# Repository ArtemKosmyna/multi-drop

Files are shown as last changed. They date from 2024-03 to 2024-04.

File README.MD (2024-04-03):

# Барабанний Скид для FPV

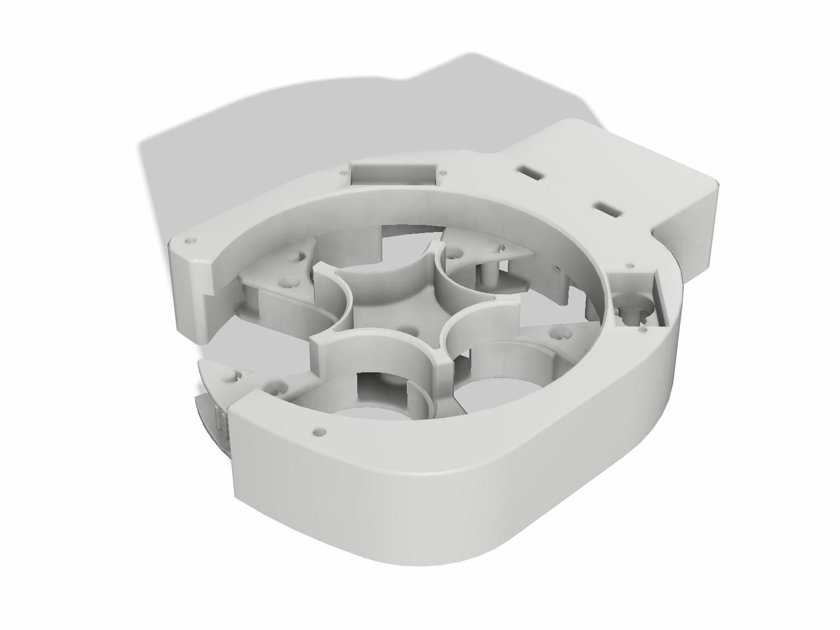
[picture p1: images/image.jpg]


## Огляд

Цей проект є барабанним скидом для FPV, розробленим для скидання 5 предметів. Він може бути монтований на дрон і управляється за допомогою сервопривода. Сам скид складається з двох основних частин: корпусу та барабану. Корпус закріплюється на дроні, тоді як барабан обертається всередині корпусу. В барабані є отвори, через які можуть випадати предмети. Сервопривід забезпечує обертання барабана та відкривання/закривання отворів.

## Інструкції зі збірки

### Налаштування друку

- Підтримка: Відсутня
- Стінки: 4 шари
- Заповнення: 20%
- Верхні/нижні стінки: 4 шари
- Матеріал: PETG

### Матеріали для VOG

- (1) БРФ_1.01.005.010_Корпус с Ардуино на 2 Холла
- (1) БРФ_1,01,005,016_Ревизия плоская
- (1) БРФ_1,01,005,013_Корпус барабана_магнит 5х2
- (2) БРФ_1,01,005,006_Шестерня привода (x,x)
- (5) БРФ_1.01.005.003_Заслонка_5stk
- (1) БРФ_1.01.005.002_Централь
- (1) БРФ_1.01.005.004_Крышка барабана
- (5) БРФ_1.01.005.005_Толкатель_5stk
- (5) БРФ_1.01.005.007_Шестерня ведомая_5stk
- (1) БРФ_1.01.005.012_Крышка под ардуино
- (4) Винти М1.4×4 для Arduino
- (15) Винти M3x8 (DIN 965 (хрест) або DIN 7991 (шестиграник)) - 15 штук

### Матеріали для 40mm

- 

### Електроніка

- (2) Сервоприводи MG-90 360 (без стопера)
- (5) Пружини d=5mm
- (2) Датчик Холла SS49E
- (1) Arduino Nano
- (2) Шлейф 3-жильний 26AWG 1м (Чорний, Червоний, Жовтий)
- (5) Магнит d=5mm, h=2mm
- (2) Термоусадкі 3=mm

### Необхідні інструменти та матеріали

- Викрутка (хрестова або плоска, залежно від кріплення корпусу серво)
- Паяльник і припій
- Електроізоляційна стрічка або термоусаджувальна трубка
- Сервотестер
- Блок живлення на 5 вольт

## Інструкції з прошивки

Цей документ містить інструкції з прошивки для Arduino Nano. Перед початком переконайтесь, що у вас встановлене середовище розробки, яке підтримує вашу Arduino Nano.

### Загальні вимоги

- Встановлене середовище [Arduino IDE](https://www.arduino.cc/en/software) або [PlatformIO](https://platformio.org/platformio-ide) для Arduino.
- USB-кабель для підключення плати до комп'ютера.
- Драйвери для вашої плати, якщо вони потрібні.

### Прошивка для Arduino

1. Відкрийте Arduino IDE.
2. Виберіть `Файл` > `Відкрити...` та знайдіть файл `firmware_(розмір_магніту).ino` у папці `arduino`.
3. Підключіть вашу п

лату Arduino до комп'ютера через USB.
4. Виберіть тип плати та порт у `Інструменти`.
5. Натисніть `Завантажити` для прошивки плати.

## Схема підключення до Arduino

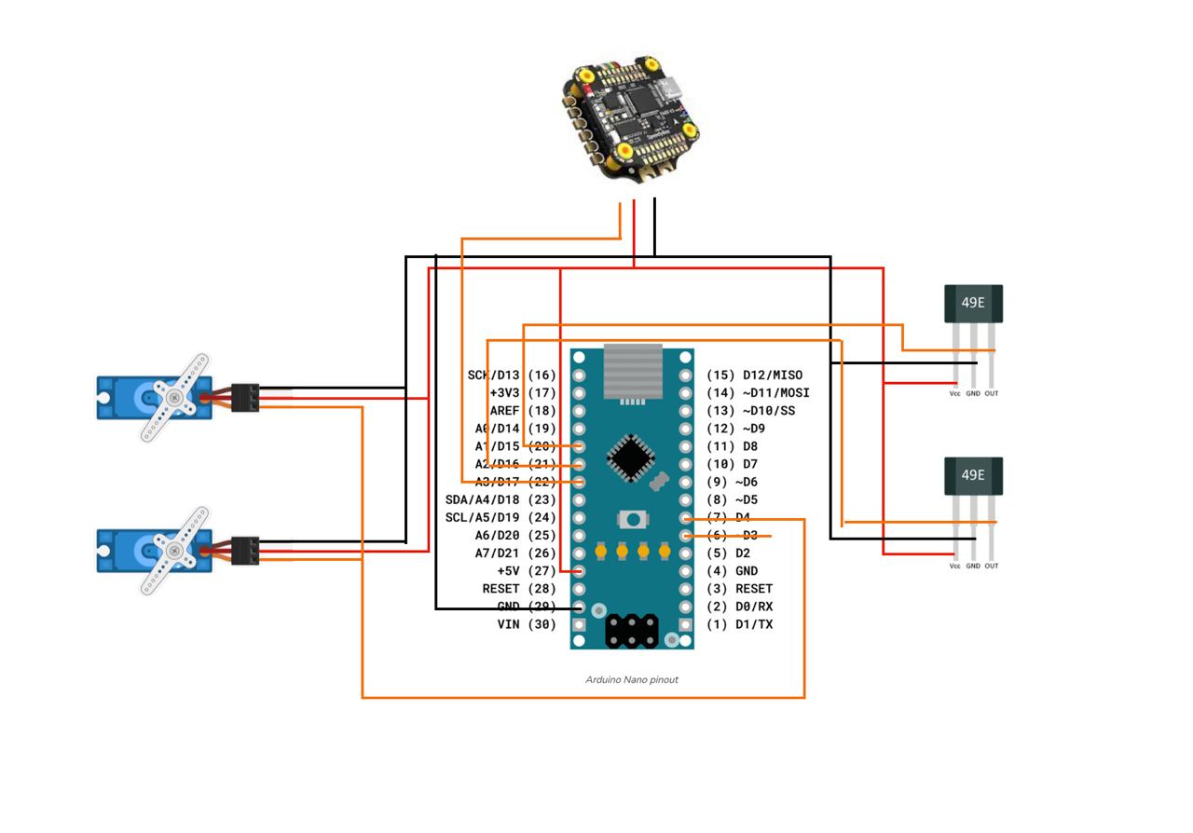
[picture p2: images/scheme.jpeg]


## Схема підключення датчиків положення

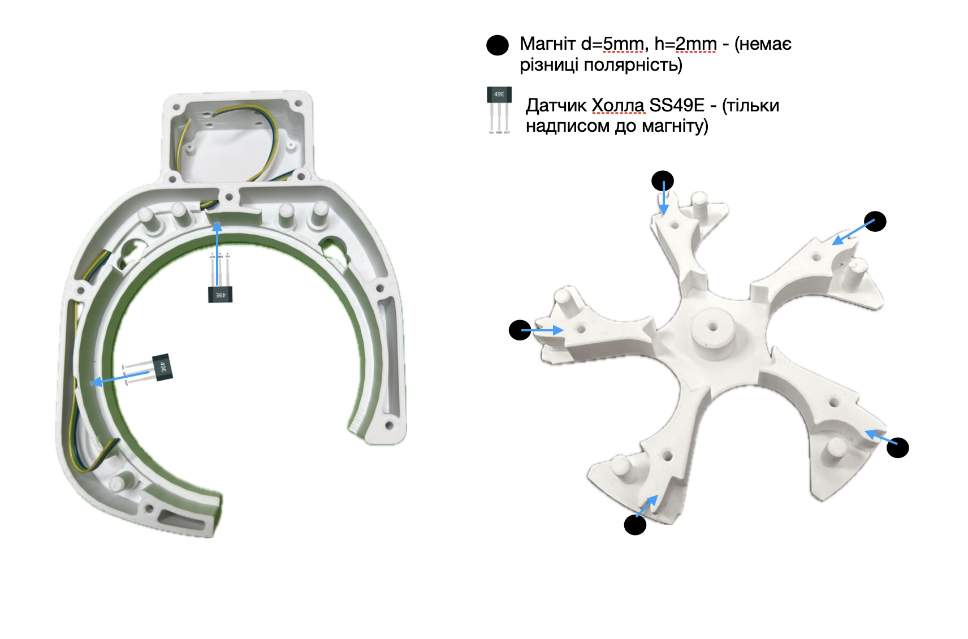
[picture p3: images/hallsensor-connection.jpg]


## Примітки

- Переконайтесь, що вибраний правильний COM-порт для вашої плати перед завантаженням.
- У деяких випадках може бути потрібно натиснути та утримувати кнопку BOOT на платі перед завантаженням або скинути плату безпосередньо після початку завантаження.

Якщо у вас виникають проблеми з підключенням або прошивкою, зверніться до офіційної документації вашої платформи.

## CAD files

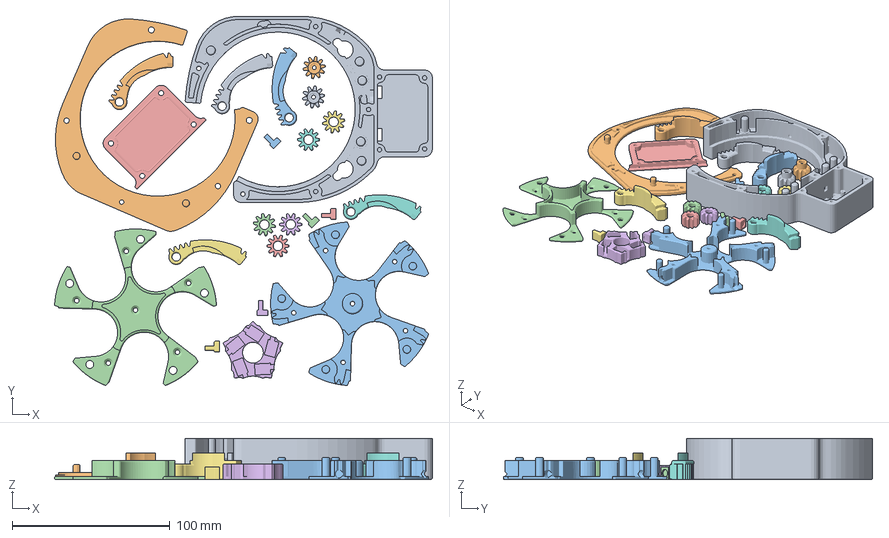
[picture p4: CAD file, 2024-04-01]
3MF/multi-drop-vog-v1.0.0.3mf
239.5 x 234.0 x 26.1 mm
БРФ_1.01.005.010_Корпус с Ардуино на 2 Холла.stl
БРФ_1.01.005.012_Крышка под ардуино.stl
БРФ_1,01,005,013_Корпус барабана_магнит 5х2.stl
БРФ_1.01.005.004_Крышка барабана.stl
БРФ_1,01,005,016_Ревизия плоская.stl
БРФ_1.01.005.002_Централь.stl
БРФ_1.01.005.003_Заслонка_5stk.stl x 5
БРФ_1.01.005.007_Шестерня ведомая_5stk.stl x 5
БРФ_1,01,005,006_Шестерня привода 4,85.stl x 2
БРФ_1.01.005.005_Толкатель_5stk.stl x 5

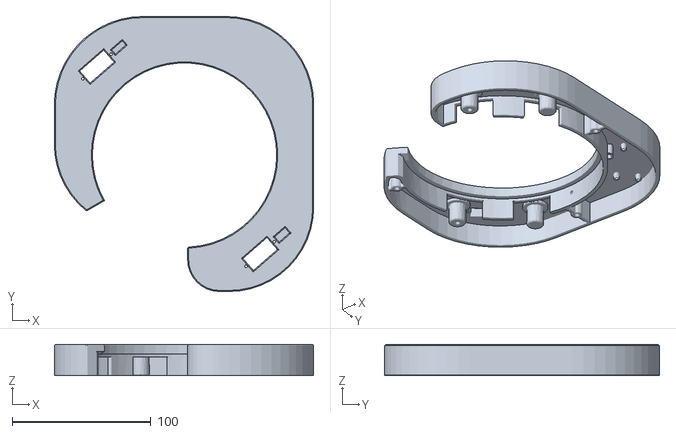
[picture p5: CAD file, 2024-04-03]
STL/40mm/БР_1,02,001,008_ Корпус_Серва.stl
187.2 x 198.5 x 22.4

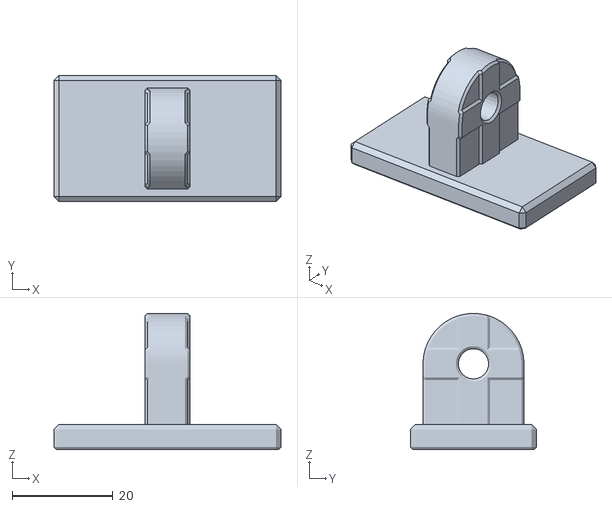
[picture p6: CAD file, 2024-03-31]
STL/VOG/БРФ_1.01.005.014_Кронштейн.stl
45.0 x 25.0 x 27.0

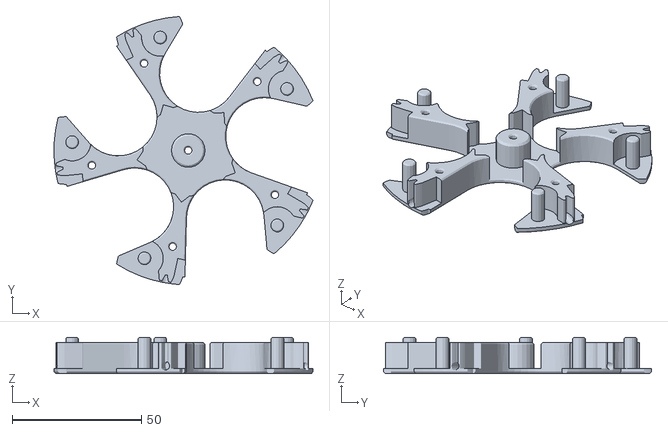
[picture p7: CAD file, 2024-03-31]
STL/VOG/Корпус барабана/БРФ_1,01,005,013_Корпус барабана_магнит 3х6.stl
100.1 x 103.6 x 14.0

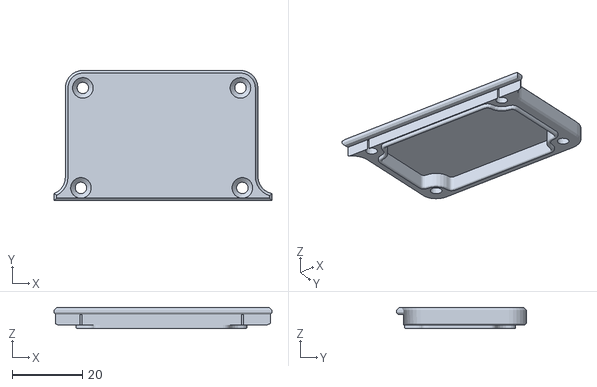
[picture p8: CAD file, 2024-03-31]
STL/VOG/Ревизия/БРФ_1,01,005,016_Ревизия плоская.stl
62.2 x 37.2 x 6.00

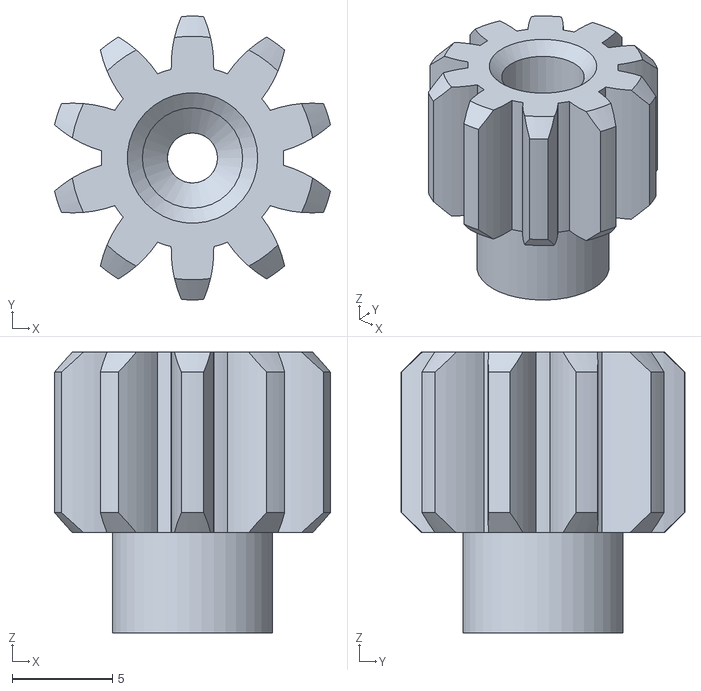
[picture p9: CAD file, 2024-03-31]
STL/VOG/Шестерня/БРФ_1,01,005,006_Шестерня привода 4,9.stl
13.8 x 14.1 x 14.0

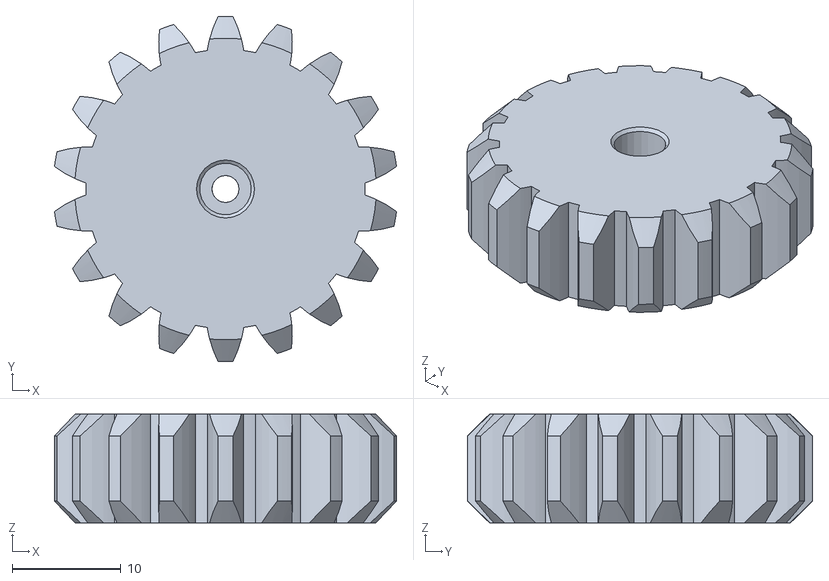
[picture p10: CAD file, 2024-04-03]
STL/40mm/БР_1,02,001,006_Шестерня привода_2шт.stl
31.5 x 31.8 x 10.0

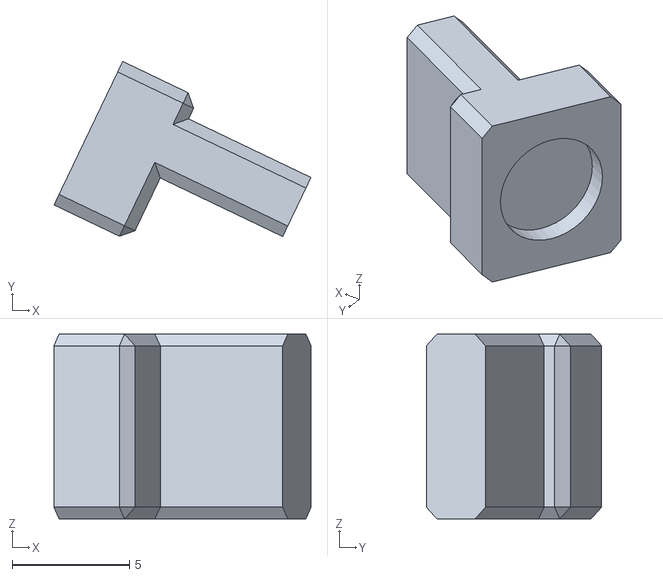
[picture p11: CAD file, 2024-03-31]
STL/VOG/БРФ_1.01.005.005_Толкатель_5stk.stl
11.0 x 7.49 x 7.90

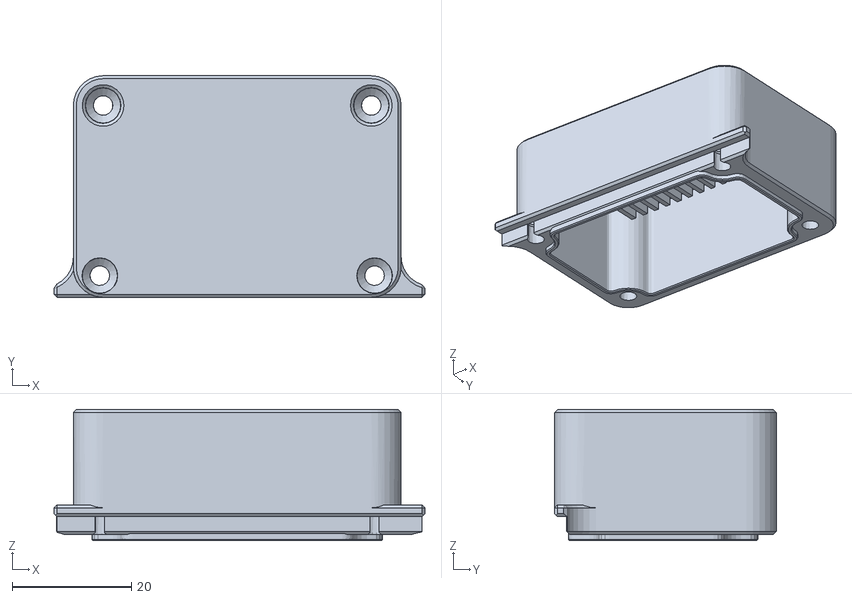
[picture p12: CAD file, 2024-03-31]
STL/VOG/Ревизия/БРФ_1,01,005,016_Ревизия с дополнительным обьемом 20мм.stl
62.2 x 37.2 x 22.0

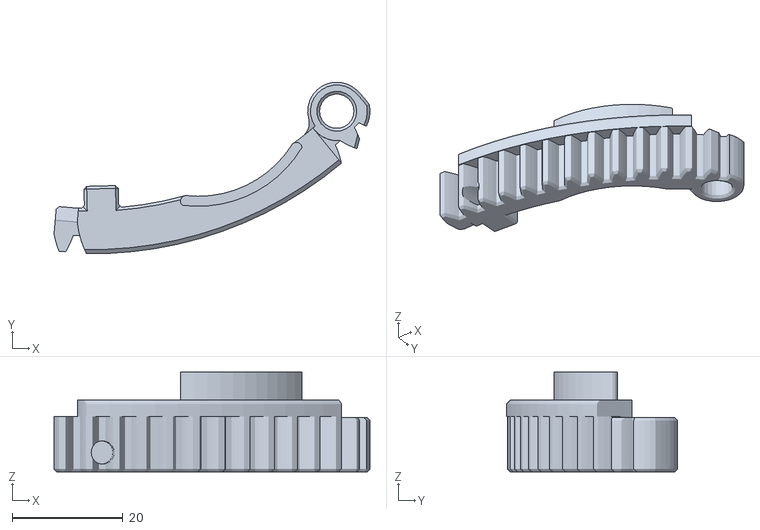
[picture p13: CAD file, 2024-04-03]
STL/40mm/БР_1,02,001,002_Заслонка барабана4х8.stl
57.0 x 30.9 x 18.0

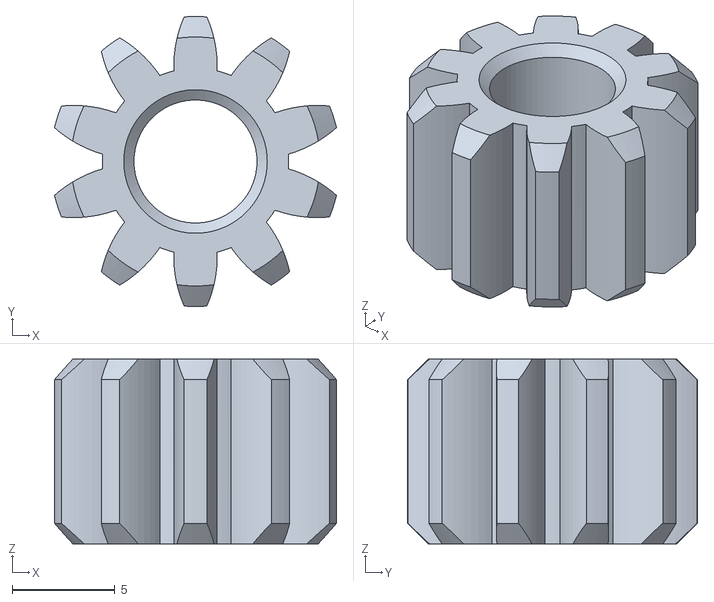
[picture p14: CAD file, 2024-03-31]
STL/VOG/БРФ_1.01.005.007_Шестерня ведомая_5stk.stl
13.8 x 14.1 x 9.00

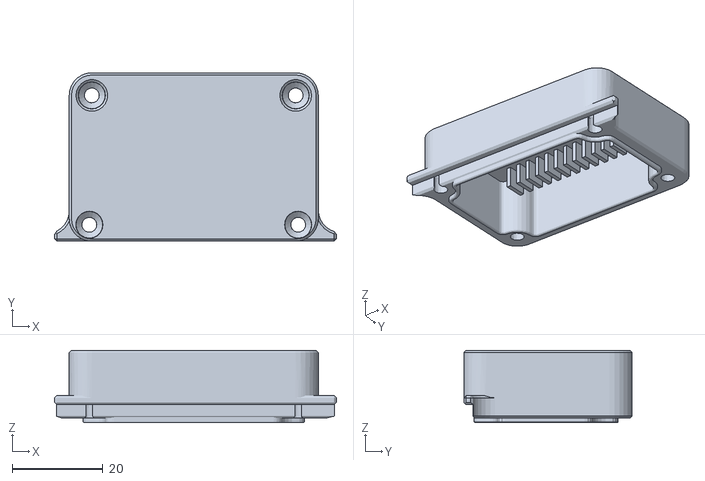
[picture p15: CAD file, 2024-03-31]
STL/VOG/Ревизия/БРФ_1,01,005,016_Ревизия с дополнительным обьемом 10 мм.stl
62.2 x 37.2 x 16.0

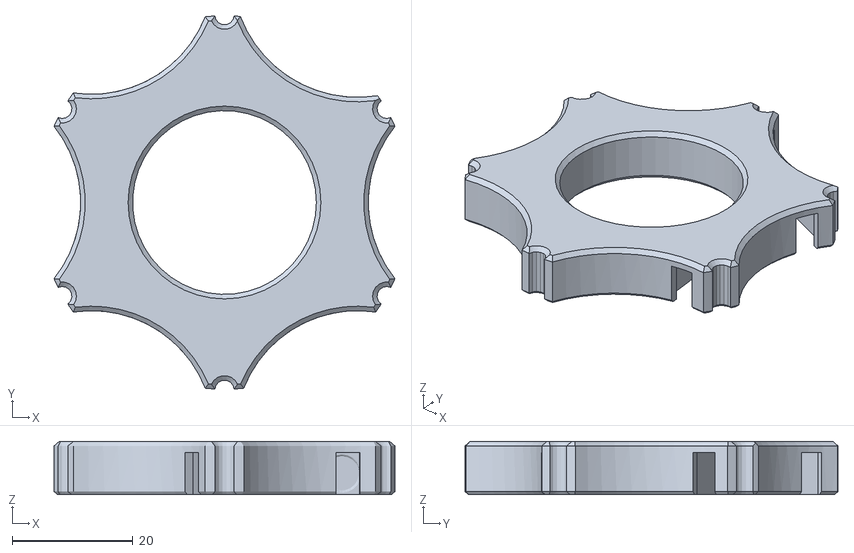
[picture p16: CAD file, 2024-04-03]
STL/40mm/БР_1,02,001,003_Централь.stl
56.4 x 61.7 x 8.80

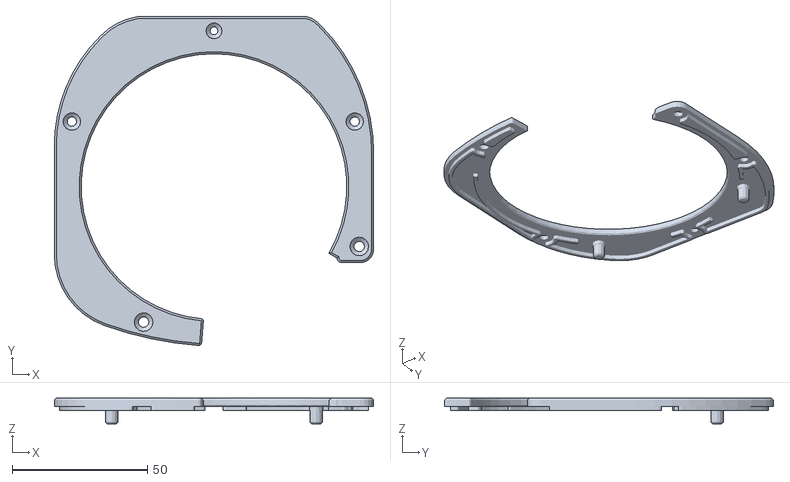
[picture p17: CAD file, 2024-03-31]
STL/VOG/БРФ_1.01.005.012_Крышка под ардуино.stl
118.0 x 121.5 x 9.50

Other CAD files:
STL/VOG/Корпус барабана/БРФ_1,01,005,013_Корпус барабана_магнит 3х4.stl
STL/VOG/Шестерня/БРФ_1,01,005,006_Шестерня привода 4,75.stl
STL/VOG/Корпус барабана/БРФ_1,01,005,013_Корпус барабана_магнит 4х8.stl
STL/VOG/Шестерня/БРФ_1,01,005,006_Шестерня привода 4,8.stl
STL/40mm/БР_1,02,001,001_Корпус барабана.stl
STL/40mm/БР_1,02,001,002_Заслонка барабана_6шт.stl
STL/40mm/БР_1,02,001,004_Толкатель_6шт.stl
STL/40mm/БР_1,02,001,005_Крышка барабана.stl
STL/40mm/БР_1,02,001,006_Шестерня привода 12GAN20_2шт.stl
STL/40mm/БР_1,02,001,007_Шестерня ведомая_4шт.stl
STL/40mm/БР_1,02,001,008_2 Корпус.stl
STL/40mm/БР_1,02,001,009_2 Крышка корпуса.stl
STL/40mm/БР_1,02,001,011_Колпачек на мотор_2шт.stl
STL/VOG/БРФ_1.01.005.002_Централь.stl
STL/VOG/БРФ_1.01.005.003_Заслонка_5stk.stl
STL/VOG/БРФ_1.01.005.004_Крышка барабана.stl
STL/VOG/БРФ_1.01.005.010_Корпус с Ардуино на 2 Холла.stl
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

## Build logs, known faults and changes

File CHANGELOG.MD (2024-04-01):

# Журнал змін

Всі важливі зміни в цьому проекті будуть документовані в цьому файлі.

Формат журналу змін базується на [Keep a Changelog](https://keepachangelog.com/),
і цей проект дотримується [Семантичного Версіонування](https://semver.org/).

## [Невипущений]

## [1.0.0] - 2024-04-31

- Переробленно STL файл з моделлю друку.
- Переробленно Arduino код.
- Видилено прошивкі під (STM32, ESP32, ESP8266).

### Додано

- Додано 3MF файл з моделлю друку.
- Додано файл з описом проекту.
- Додано файл з журналом змін.
- Додано файл з ліцензією проекту.
- Додано файл з описом встановлення проекту.
- Додано файл з описом використання проекту.

## [0.1.0] - 2024-01-20

### Додано

- Початковий реліз проекту.

### Змінено

### Виправлено

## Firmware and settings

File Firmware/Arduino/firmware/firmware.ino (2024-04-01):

// Version 1.0.0

#include <Servo.h>

Servo myservo;

const int servoPin = 4;
const int positionMove = 700;
const int positionStop = 1500;
const int minMagnet = 514;
const int maxMagnet = 525;

const int hallSensorOpenPin = 2;
const int hallSensorClosedPin = 1;

const int activationPin = A3;

bool lastSignalState = false;
bool closedStateDetected = false;
bool openStateDetected = false;
int refilled = 5;
bool refillCompleted = false;

bool dropActive = false;

bool processSignal() {
    static int thresholdOn = 1900;
    static int thresholdOff = 1000;
    int duration = pulseIn(activationPin, HIGH);

    if (duration > thresholdOn && !lastSignalState) {
        lastSignalState = true;
        Serial.println("Rotate");
        return true;
    } else if (duration < thresholdOff && lastSignalState) {
        lastSignalState = false;
    }
    return false;
}

int readHallSensor(int pin) {
    return analogRead(pin);
}

void setup() {
    myservo.attach(servoPin);
    pinMode(hallSensorOpenPin, INPUT);
    pinMode(hallSensorClosedPin, INPUT);
    Serial.begin(9600);
    Serial.println("---------- Multi Drop Version 1.0.0 ------------");
}

void loop() {
    int closedStateValue = readHallSensor(hallSensorClosedPin);
    int openStateValue = readHallSensor(hallSensorOpenPin);

    if (closedStateValue < minMagnet || closedStateValue > maxMagnet) {
        closedStateDetected = true;
    }

    if (openStateValue < minMagnet || openStateValue > maxMagnet) {
        openStateDetected = true;
    }

    delay(20); // Delay to prevent excessive servo movement or signal processing

    if (refilled != 0) {
        if (processSignal() && refilled > 0) {
            Serial.println("Refill Started");
            myservo.writeMicroseconds(positionMove);
        }

        if (refilled != 0 && closedStateDetected && (openStateValue < minMagnet || openStateValue > maxMagnet)) {
            Serial.println("Refill Waiting");
            Serial.println(closedStateValue);
            Serial.println(openStateValue);
            myservo.writeMicroseconds(positionStop);
            refilled--;
            closedStateDetected = false;
        }

        if (refilled == 0) {
            Serial.println("Refill Completed");
            Serial.println(refilled);
            refillCompleted = true;
        }
    }

    if (refillCompleted) {
        if (processSignal()) {
            Serial.println("Drop started");
            myservo.writeMicroseconds(positionMove);
            dropActive = true;
        }
        if (openStateDetected && (closedStateValue < minMagnet || closedStateValue > maxMagnet)) {
            Serial.println("Drop activated");
            Serial.println(closedStateValue);
            Serial.println(openStateValue);
            myservo.writeMicroseconds(positionStop);
            openStateDetected = false;
        }
    }
}

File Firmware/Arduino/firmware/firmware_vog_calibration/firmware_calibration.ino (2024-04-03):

#include <Servo.h>

Servo myservo;

const int servoPin = 4;
const int positionMove = 700; 
const int positionStop = 1500;

const int hallSensorOpenPin = 2;
const int hallSensorClosedPin = 3;

const int activationPin = A1;

unsigned long startTime;
const long calibrationPeriod = 10000;
bool calibrationCompleted = false;
int minMagnetValue = 1023;
int maxMagnetValue = 0;


int readHallSensor(int pin) {
    return analogRead(pin);
}

void setup() {
    myservo.attach(servoPin);
    pinMode(hallSensorOpenPin, INPUT);
    pinMode(hallSensorClosedPin, INPUT);
    Serial.begin(9600);
    Serial.println("---------- Multi Drop Calibration Version 1.0.0 ------------");
    startTime = millis(); 
}

void loop() {
    if (!calibrationCompleted) {
        if (millis() - startTime < calibrationPeriod) {
           
            myservo.writeMicroseconds(positionMove);
            
            int sensorValue = readHallSensor(hallSensorClosedPin);
            minMagnetValue = min(minMagnetValue, sensorValue);
            maxMagnetValue = max(maxMagnetValue, sensorValue);
        } else {
            myservo.writeMicroseconds(positionStop);
            calibrationCompleted = true;
            Serial.print("Calibration Completed. Min: ");
            Serial.print(minMagnetValue);
            Serial.print(", Max: ");
            Serial.println(maxMagnetValue);
        }
    }

}

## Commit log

2024-02-12 fix: basic frame project
    [katushka-sbros.3mf]
2024-02-13 add: instruction how to rework servo
2024-02-24 fix: parts
    [Korpus_niz_v2.stl, Korpus_verh_v2.stl, baraban_nis_v2.stl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]
2024-02-24 remove: outdated project
    [cylinder-drop-fpv v1.f3d]
2024-03-31 [release] 1.0.0
    [basic.stl, БР_1,01,002,001_Шестерня привода.stl, БР_1,01,002,002_Барабан.stl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]
2024-03-31 3mf new
    [katushka-sbros.3mf]
2024-04-01 add: 3mf
    [multi-drop-v1.0.0.3mf]
2024-04-01 remove: old 3mf
    [katushka-sbros.3mf]
2024-04-03 add 40mm and 4x8 and 5x2 and calib
    [БР_1,02,001,001_Корпус барабана.stl, БР_1,02,001,002_Заслонка барабана_6шт.stl, БР_1,02,001,003_Централь.stl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]
2024-04-03 add 4x8 calibrated
2024-04-03 add: missing parts
    [БР_1,02,001,002_Заслонка барабана4х8.stl]
2024-04-03 add: missing parts MG90 40mm
    [БР_1,02,001,006_Шестерня привода_2шт.stl, БР_1,02,001,008_ Корпус_Серва.stl]
